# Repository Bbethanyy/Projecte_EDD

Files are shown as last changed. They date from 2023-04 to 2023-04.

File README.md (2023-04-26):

View this project on [CADLAB.io](https://cadlab.io/project/26669). 

# Projecte EDD: Disseny eletrònic d'un maleter
**Membres del grup:** Jan Castillo, Bethany Quintero
----------------------------------------------------
## Objectiu
Dissenyar un sistema electrònic capaç d'obrir un maleter d'un automòbil utilitzant un sensor de proximitat i que pogui escalfar el vidre que l'acompanya.

## Requisits/Especificacions
- Microcontrolador 
- Dos reguladors de tensions: un pel microcontrolador i l'altre per al sensor
- Sensor de proximitat per detectar un gest amb el peu 
- Resistèncias calefactores per escalar el vidre
- Driver per controlar el Brushless DC motor per obrir i tancar el maleter
- Resistor shunt per indicar el final de la carerra
- Connectors

## Diagrama de blocs


## Components
| Ref. | Descripció| Datasheet |
| --- | ---| ---|
|PIC18F258|Microcontrolador|[Datasheet](https://www.mouser.es/datasheet/2/268/41159e-30206.pdf)|
|LM1117|Regulador de tensió|[Datasheet](https://www.ti.com/lit/ds/snos412q/snos412q.pdf?ts=1679503528555&ref_url=https%253A%252F%252Fwww.ti.com%252F)|
|FDC2212|Sensor de proximitat|[Datasheet](https://www.ti.com/lit/ds/symlink/fdc2212-q1.pdf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)|
|MCP2551|Transceiver|[Datasheet](https://www.mouser.es/datasheet/2/268/20001667G-1115479.pdf)|
|ECS-80-20-20A-TR|Oscillador|[Datasheet](https://ecsxtal.com/store/pdf/csm-8r.pdf)|
|PSR100|Shunt resistor|[Datasheet](https://fscdn.rohm.com/en/products/databook/datasheet/passive/resistor/chip_resistor/psr-e.pdf)|
|AD8616|OpAmp|[Datasheet](https://www.analog.com/media/en/technical-documentation/data-sheets/AD8615_8616_8618.pdf)|
|ADW1112W|Relé|[Datasheet](https://www.datasheetq.com/datasheet-download/853198/1/Panasonic/ADW1112W)|
|1393280-5|Relé micro K|[Datasheet](https://www.te.com/commerce/DocumentDelivery/DDEController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)|
|BLDC-48|Brushless motor|[Datasheet](https://www.farnell.com/datasheets/526541.pdf)|
|GBR-612|Heating Element|[Datasheet](https://www.tme.eu/Document/745dece1e8a1927996aa7af3a5cfc3a0/GBR-612_ENG.pdf)|
|BC 817/25|BJT|[Datasheet](https://pdf1.alldatasheet.com/datasheet-pdf/view/16111/PHILIPS/BC817-25.html)|
|TCA39306|Level Shifter|[Datasheet](https://www.ti.com/lit/ds/symlink/tca39306.pdf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)|

## Simulacions
Anem a veure diferents simulacions que hem pogut fer amb LTSPICE per comprovar el correcte funcionament del projecte.
### Reguladors de tensió
El primer a simular ha estat els reguladors de tensió a utilitzar, una de les més senzilles:


I podem comprovar que els potencials als nodes són els dessitjats:



### Relé
Malauradament LTSPICE no té relés. Hem utilitzat un interruptor per tensió i hem aproximat alguns dels seus paràmetres al nostre relé, per a fer una simulació aproximada:



I així, podem comprovar que passa la tensió dessitjada:



### Control de corrent
L'últim sistema que podem simular és el sistema d'amplificadors operacionals que permetran regular el corrent del motor i, per tant, el final de carrera d'aquest:



Aleshores es pot comprovar que si la font és de 1.33 A (funcionament normal), la sortida és el valor baix de saturació:



I en canvi, si la font és de 1.95 A (realment es retallaria abans), la sortida serà el valor alt de tensió:



## Esquemàtic


## Layout


## 3D Model


## Costos finals:
|Cantitat de PCBs| Preu |Stencil|
| --- | ---| ---|
|10|562,668 €|No|
|50|2520,3 €|Sí|
|1000|36316,84 €|Sí|
|20000|709205,21 €|Sí|

## Historial de canvis
|Data| Autor/a |Descripció|
| --- | ---| ---|
|23/03/23|Bethany Quintero i Jan Castillo|Segona versió diagrama de blocs i selecció de components|
|23/03/23|Bethany Quintero i Jan Castillo|Correcció diagrama de blocs i afegit el BJT a components|
|26/03/23|Jan Castillo|Actualització diagrama de blocs i components (OPAMP). Afegides les simulacions i els resultats|
|27/03/23|Jan Castillo|Actualització de components (driver canviat per relés) i, per tant, actualitzat també el diagrama de blocs. Actualització de la simulació del final de carrera|
|27/03/23| Bethany Quintero | Primera versió de l'esquemàtic|
|28/03/23| Bethany Quintero | Correcció del driver i afegits els valors dels components que faltaven a l'esquemàtic|
|1/04/23| Jan Castillo |Afegit Level Shifter a components. Actualització del diagrama de blocs i canviat el valor Vref de la simulació del final de carrera.|
|2/04/23| Jan Castillo |Canviat Level Shifter i, per tant, el diagrama de blocs.|
|5/04/23| Bethany Quintero | Canviat el model del level shifter. Actualització esquemàtic: afegits els divisors de tensions per Vref i level shifter.|
|6/04/23| Jan Castillo | Alguns canvis a l'esquemàtic.|
|6/04/23| Bethany Quintero | Canvi a l'esquemàtic.|
|9/04/23| Bethany Quintero | Canvi de nets a l'esquemàti.c|
|10/04/23| Jan Castillo i Bethany Quintero |Primera versió Layout.|
|23/04/23| Jan Castillo i Bethany Quintero |Actualització diagrama de blocs, esquemàtic i layout finals.|
|25/04/23| Jan Castillo i Bethany Quintero |Afegit de pressupostos i petits canvis al layout.|

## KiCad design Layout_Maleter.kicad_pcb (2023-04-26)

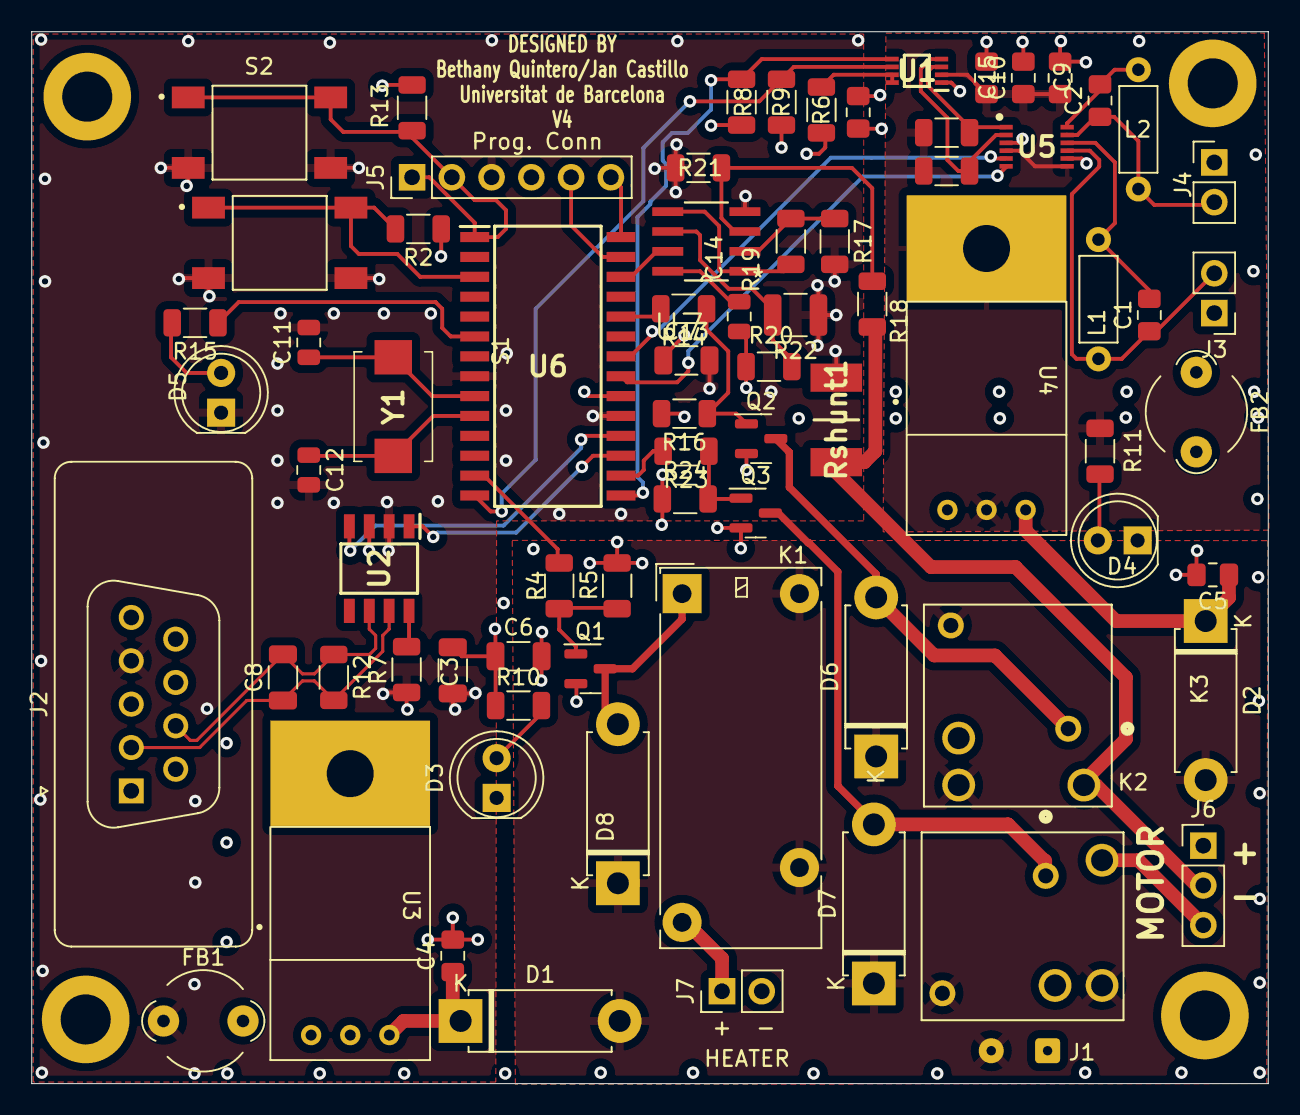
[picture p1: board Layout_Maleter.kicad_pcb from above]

Board: 4 copper layers, 79.0 x 67.2 mm, 75 parts (0 on the bottom side), 51 nets.

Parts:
C1, C2: 33pF; C_0805_2012Metric_Pad1.18x1.45mm_HandSolder
C3, C13: 100nF; C_1206_3216Metric
C4, C5: 10uF; C_0805_2012Metric_Pad1.18x1.45mm_HandSolder
C6: 10uF; C_1206_3216Metric
C8: 100pF; C_1206_3216Metric
C9, C15, C16: 0.1 uF; C_0805_2012Metric_Pad1.18x1.45mm_HandSolder
C10: 0.1uF; C_0805_2012Metric_Pad1.18x1.45mm_HandSolder
C11, C12: 15 pF; C_0805_2012Metric
C14: 100 nF; C_0805_2012Metric
D1, D2, D6, D7, D8: 1N4002; D_5W_P10.16mm_Horizontal
D3, D4, D5: LED; LED_D5.0mm
FB1, FB2: FerriteBead_Small; LairdTech_28C0236-0JW-10
J1: Conn_01x02; SolderWire-0.1sqmm_1x02_P3.6mm_D0.4mm_OD1mm
J2: DB9_Male; DSUB-9_Male_Vertical_P2.77x2.84mm
J3, J4, J7: Conn_01x02; PinHeader_1x02_P2.54mm_Vertical
J5: Conn_01x06_Fem; PinHeader_1x06_P2.54mm_Vertical
J6: Conn_Male; PinHeader_1x03_P2.54mm_Vertical
K1: ADW11; Relay_1P1T_NO_10x24x18.8mm_Panasonic_ADW11xxxxW_THT
K2, K3: 1393280-5; RELAY_1393280-5
L1, L2: 18uH; L_Axial_L5.3mm_D2.2mm_P7.62mm_Horizontal_Vishay_IM-1
Q1, Q2, Q3: BC817; SOT-23
R1, R3, R8, R9: 22k; R_1206_3216Metric
R2, R13: 10K; R_1206_3216Metric
R4, R14, R23: 60k; R_1206_3216Metric
R5, R16, R20, R24: 10k; R_1206_3216Metric
R6: 200k; R_1206_3216Metric
R7: 20k; R_1206_3216Metric
R10, R11, R15, R17, R18: 1k; R_1206_3216Metric
R12: 60; R_1206_3216Metric
R19, R21: 100k; R_1206_3216Metric
R22: 120k; R_1210_3225Metric
Rshunt1: 2m; ShuntRes
S1, S2: 2-1437565-7; SW_2-1437565-7
U1: TCA39306DTMR; SOP50P310X90-8N
U2: MCP2551-I-P; TRANSCEIVER_SMD
U3: LM1117-5.0; TO-220
U4: LM1117-3.3; TO-220
U5: FDC2212QDNTTQ1; SON50P400X400X100-13N
U6: PIC18F258-I/SP; MICROSMD
U7: AD8616ARZ; SOIC127P600X175-8N
Y1: Crystal; CRISTALL

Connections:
+VCC1: C3.1, C6.1, C13.1, C14.1, C16.1, J5.4, R2.1, R6.1, R8.1, R9.1, R10.1, R13.1, R20.1, U2.3 (VDD), U3.2 (VO), U3.4, U6.20 (VDD)
+VCC2: C9.1, C10.1, C15.1, R1.1, R3.1, R11.1, U1.2 (VREF1), U4.2 (VO), U4.4, U5.4 (ADDR), U5.7 (VDD)
/CAN+: C8.1, J2.2, R12.2, U2.7 (CANH)
/CAN-: C8.2, J2.7, R12.1, U2.6 (CANL)
/Heater: R2.2, S1.1, S1.2, U6.3 (RA1/AN1)
/INTB: U5.5 (INTB), U6.22 (RB1/INT1)
/IN_B: R19.2, U7.1 (OUT_A), U7.5 (+INB)
/OSC1: C11.1, U6.9 (OSC1/CLKI), Y1.1
/OSC2: C12.1, U6.10 (OSC2/CLKO/RA6), Y1.2
/PGC: J5.5, U6.27 (RB6/PGC)
/PGD: J5.6, U6.28 (RB7/PGD)
/PMW_5V: R4.2, U6.13 (RC2/CCP1)
/RESET: J5.1, J5.2, R13.2, S2.1, S2.2, U6.1 (~MCLR/VPP)
/RX_CAN: U2.4 (RXD), U6.18 (RC7/RX/DT)
/Relé1: R14.2, U6.24 (RB3/CANRX)
/Relé2: R23.2, U6.16 (RC5/SDO)
/SCL1: R1.2, U1.3 (SCL1), U5.1 (SCL)
/SCL2: R9.2, U1.6 (SCL2), U6.14 (RC3/SCK/SCL)
/SD: U5.6 (SD), U6.21 (RB0/INT0)
/SDA1: R3.2, U1.4 (SDA1), U5.2 (SDA)
/SDA2: R8.2, U1.5 (SDA2), U6.15 (RC4/SDI/SDA)
/TX_CAN: U2.1 (TXD), U6.17 (RC6/TX/CK)
GND: C3.2, C9.2, C10.2, C11.2, C12.2, C13.2, C15.2, C16.2, D5.1 (K), FB1.1, FB2.1, J1.1, J2.4, J3.1, J4.1, J5.3, R7.1, R17.2, R21.1, R22.1, Rshunt1.2, S1.3, S1.4, S2.3, S2.4, U1.1 (GND), U2.2 (VSS), U5.3 (CLKIN), U5.8 (GND), U6.8 (VSS), U6.19 (VSS), U7.4 (V-)
GNDPWR: C4.2, C5.2, C6.2, D3.1 (K), D4.1 (K), FB1.2, FB2.2, J6.1, J7.2, K2.5, K3.5, Q1.2 (E), Q2.2 (E), Q3.2 (E), R5.2, R16.2, R24.1, U3.1 (GND), U4.1 (GND)
INTERRP: U6.26 (RB5/PGM), U7.7 (OUT_B)
M1: J6.2, K2.4, R18.2, Rshunt1.1
M2: J6.3, K3.4
unnamed: C1.1, J3.2, L1.1, U5.9 (IN0A)
unnamed: C1.2, L1.2, U5.10 (IN0B)
unnamed: C2.1, J4.2, L2.1, U5.11 (IN1A)
unnamed: C2.2, L2.2, U5.12 (IN1B)
unnamed: C4.1, D1.1 (K), U3.3 (VI)
unnamed: C5.1, D2.1 (K), U4.3 (VI)
unnamed: C14.2, U7.8 (V+)
unnamed: D3.2 (A), R10.2
unnamed: D4.2 (A), R11.2
unnamed: D5.2 (A), R15.2
unnamed: D6.2 (A), K2.1, Q2.3 (C)
unnamed: D7.2 (A), K3.1, Q3.3 (C)
unnamed: D8.2 (A), K1.1, Q1.3 (C)
unnamed: J7.1, K1.3
unnamed: Q1.1 (B), R4.1, R5.1
unnamed: Q2.1 (B), R14.1, R16.1
unnamed: Q3.1 (B), R23.1, R24.2
unnamed: R6.2, U1.7 (VREF2), U1.8 (EN)
unnamed: R7.2, U2.8 (Rs)
unnamed: R15.1, U6.6 (RA4/T0CKI)
unnamed: R17.1, R19.1, U7.2 (-INA)
unnamed: R18.1, R21.2, U7.3 (+INA)
unnamed: R20.2, R22.2, U7.6 (-INB)
VBAT: D1.2 (A), D2.2 (A), D6.1 (K), D7.1 (K), D8.1 (K), J1.2, K1.5, K1.6, K2.2, K2.3, K3.2, K3.3
